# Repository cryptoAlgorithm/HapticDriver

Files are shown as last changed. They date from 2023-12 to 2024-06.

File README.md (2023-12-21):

# HapticDriver

> Compact and over-engineered solenoid driver board for the purpose of generating localised haptic feedback.

## Features

* ESP32S3 module
* USB-C host port
* 12 MOSFET H-bridges with current regulation (up to 1A each)
* Powered by LiPo batteries (15V max)
* Extremely compact size - approx 6x3cm including antenna
* 4-layer PCB

---

## Description

This is a _work in progress_ driver board which has the capability to drive 12 solenoids bi-directionally
for the purpose of providing focused and precise haptic feedback. It's intended to be used in tendem with
a host application communicating over either WiFi or Bluetooth.

Due to the ESP module's limited number of GPIO, 3 8-bit shift registers over I2S were used to effectively
expand 3 I2S GPIO into 24 individually assignable outputs. This corresponds to the 24 H-bridge driver
inputs, which allow powering 12 electromagnets (forming solenoids) with regulated current of either
direction.

There is a 3V3 LDO regulator onboard for powering the logic bus - including the ESP32, shift registers
and motor driver logic power. It's powered through the battery power input, and provides up to 800mA and
has an absolute maximum voltage of 15V. Although the drivers tolerate a power input of up to 18V, the
LDO effectively limits the maximum battery input voltage to 15V. Care should be taken not to exceed this.

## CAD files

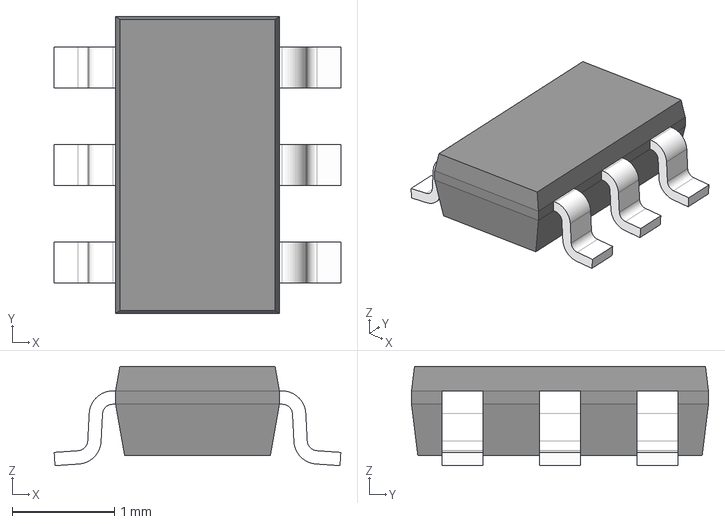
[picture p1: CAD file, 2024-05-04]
3DModels/DDC0006A.step
2.80 x 2.90 x 0.97 mm
BODY-SOT
LEAD-SOT x 6

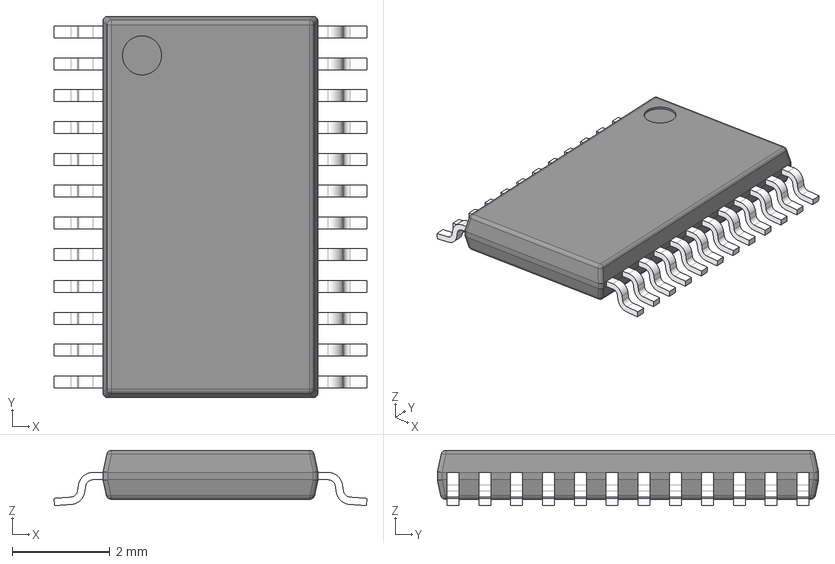
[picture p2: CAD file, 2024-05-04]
3DModels/PWP0024M.step
6.40 x 7.80 x 1.13 mm
BODY-TSSOP
LEAD-TSSOP x 24
PIN1
DAP

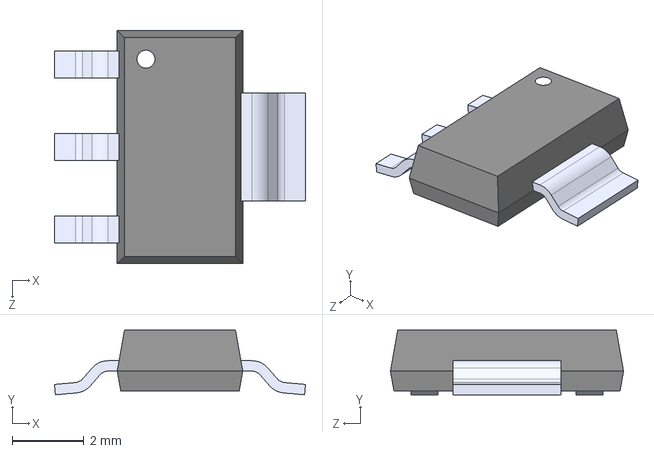
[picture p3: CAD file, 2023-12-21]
3DModels/REG1117-3.3.step
7.00 x 1.80 x 6.50 mm

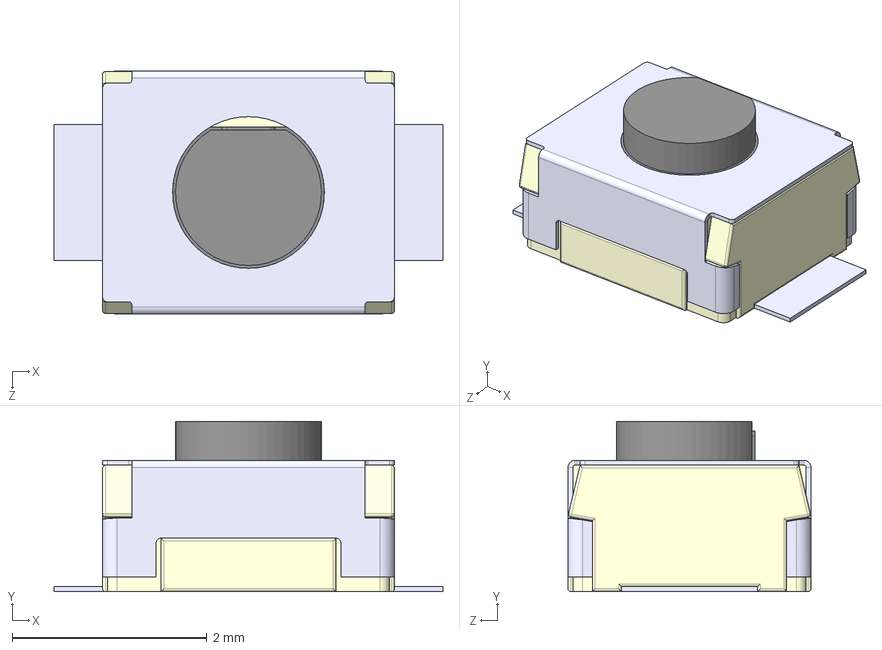
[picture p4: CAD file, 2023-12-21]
3DModels/B3U-1000P.step
4.00 x 1.75 x 2.50 mm

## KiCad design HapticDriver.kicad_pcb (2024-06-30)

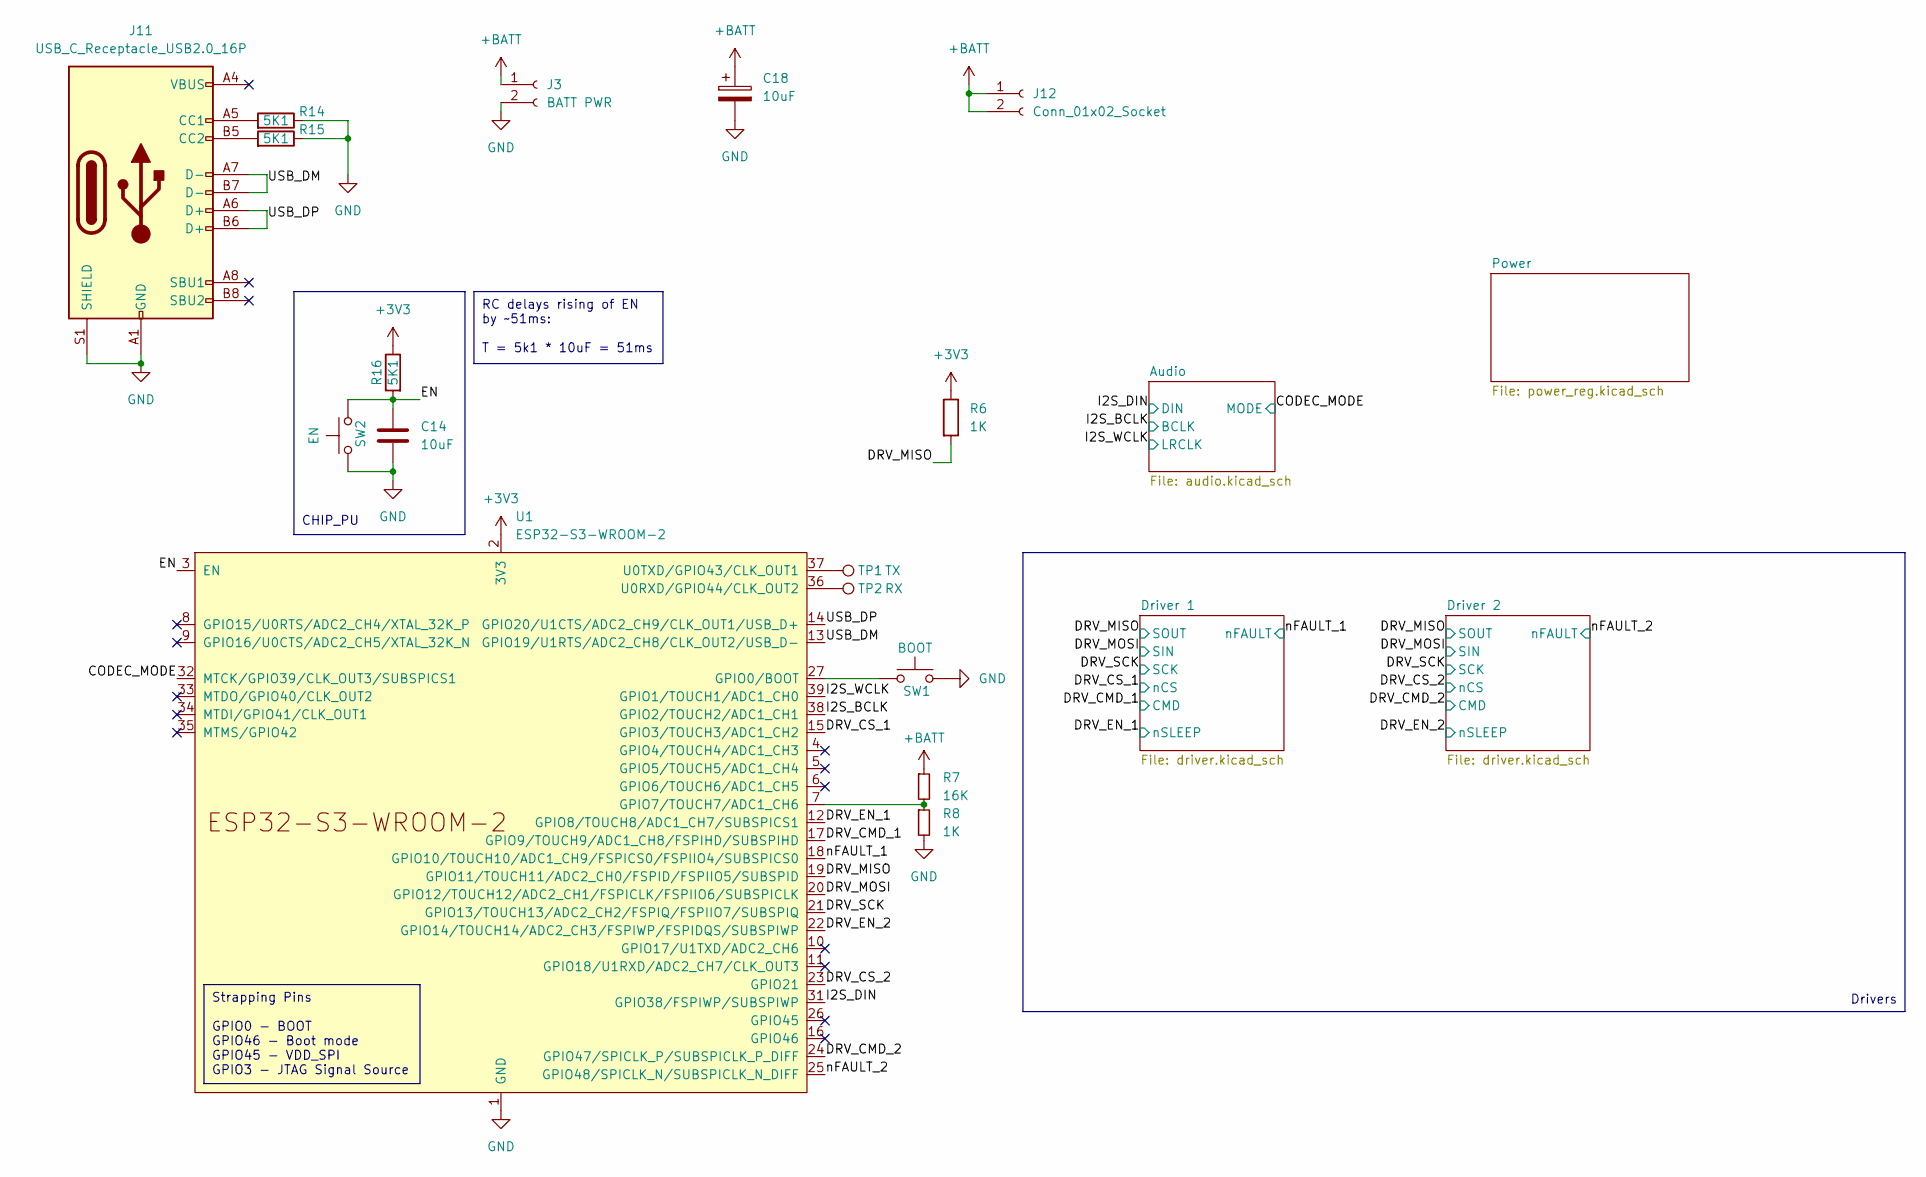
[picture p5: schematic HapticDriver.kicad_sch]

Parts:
C14: 10uF; C_0603_1608Metric; Part C96446
C18: 10uF; CP_Elec_4x5.4; Part C3001227
J3: BATT PWR; SolderWire-1sqmm_1x02_P5.4mm_D1.4mm_OD2.7mm
J11: USB_C_Receptacle_USB2.0_16P; USB_C_Receptacle_G-Switch_GT-USB-7010ASV; Part C2988369
J12: Conn_01x02_Socket; SolderWire_1x02
R6, R8: 1K; R_0402_1005Metric; Part C11702
R7: 16K; R_0402_1005Metric; Part C543609
R14, R15, R16: 5K1; R_0603_1608Metric; Part C2889415
SW1: BOOT; SW_Push_1P1T_XKB_TS-1187A; Part C318884
SW2: EN; SW_Push_1P1T_XKB_TS-1187A; Part C318884
TP1: TX; TestPoint_Pad_1.5x1.5mm
TP2: RX; TestPoint_Pad_1.5x1.5mm
U1: ESP32-S3-WROOM-2; ESP32-S3-WROOM-1; Part C2913202

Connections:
+3V3: R6.1, R16.1, U1.2 (3V3); also elsewhere on the board
+BATT: C18.1, J3.1, J12.1, J12.2, R7.1; also elsewhere on the board
/CODEC_MODE: U1.32 (MTCK/GPIO39/CLK_OUT3/SUBSPICS1); also elsewhere on the board
/DRV_CMD_1: U1.17 (GPIO9/TOUCH9/ADC1_CH8/FSPIHD/SUBSPIHD); also elsewhere on the board
/DRV_CMD_2: U1.24 (GPIO47/SPICLK_P/SUBSPICLK_P_DIFF); also elsewhere on the board
/DRV_CS_1: U1.15 (GPIO3/TOUCH3/ADC1_CH2); also elsewhere on the board
/DRV_CS_2: U1.23 (GPIO21); also elsewhere on the board
/DRV_EN_1: U1.12 (GPIO8/TOUCH8/ADC1_CH7/SUBSPICS1); also elsewhere on the board
/DRV_EN_2: U1.22 (GPIO14/TOUCH14/ADC2_CH3/FSPIWP/FSPIDQS/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); also elsewhere on the board
/DRV_MISO: R6.2, U1.19 (GPIO11/TOUCH11/ADC2_CH0/FSPID/FSPIIO5/S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); also elsewhere on the board
/DRV_MOSI: U1.20 (GPIO12/TOUCH12/ADC2_CH1/FSPICLK/FSPIIO6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); also elsewhere on the board
/DRV_SCK: U1.21 (GPIO13/TOUCH13/ADC2_CH2/FSPIQ/FSPIIO7/S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); also elsewhere on the board
/EN: C14.1, R16.2, SW2.2, U1.3 (EN)
/I2S_BCLK: U1.38 (GPIO2/TOUCH2/ADC1_CH1); also elsewhere on the board
/I2S_DIN: U1.31 (GPIO38/FSPIWP/SUBSPIWP); also elsewhere on the board
/I2S_WCLK: U1.39 (GPIO1/TOUCH1/ADC1_CH0); also elsewhere on the board
/USB_DM: J11.A7 (D-), J11.B7 (D-), U1.13 (GPIO19/U1RTS/ADC2_CH8/CLK_OUT2/USB_D-)
/USB_DP: J11.A6 (D+), J11.B6 (D+), U1.14 (GPIO20/U1CTS/ADC2_CH9/CLK_OUT1/USB_D+)
/nFAULT_1: U1.18 (GPIO10/TOUCH10/ADC1_CH9/FSPICS0/FSPIIO4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); also elsewhere on the board
/nFAULT_2: U1.25 (GPIO48/SPICLK_N/SUBSPICLK_N_DIFF); also elsewhere on the board
GND: C14.2, C18.2, J3.2, J11.A1 (GND), J11.A12 (GND), J11.B1 (GND), J11.B12 (GND), J11.S1 (SHIELD), R8.2, R14.1, R15.1, SW1.2, SW2.1, U1.1 (GND), U1.40 (GND), U1.41 (GND); also elsewhere on the board
unnamed: J11.A5 (CC1), R14.2
unnamed: J11.B5 (CC2), R15.2
unnamed: SW1.1, U1.27 (GPIO0/BOOT)
unnamed: R7.2, R8.1, U1.7 (GPIO7/TOUCH7/ADC1_CH6)
unnamed: TP2.1, U1.36 (U0RXD/GPIO44/CLK_OUT2)
unnamed: TP1.1, U1.37 (U0TXD/GPIO43/CLK_OUT1)

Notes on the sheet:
Strapping Pins GPIO0 - BOOT GPIO46 - Boot mode GPIO45 - VDD_SPI GPIO3 - JTAG Signal Source
RC delays rising of EN by ~51ms: T = 5k1 * 10uF = 51ms
Drivers
CHIP_PU

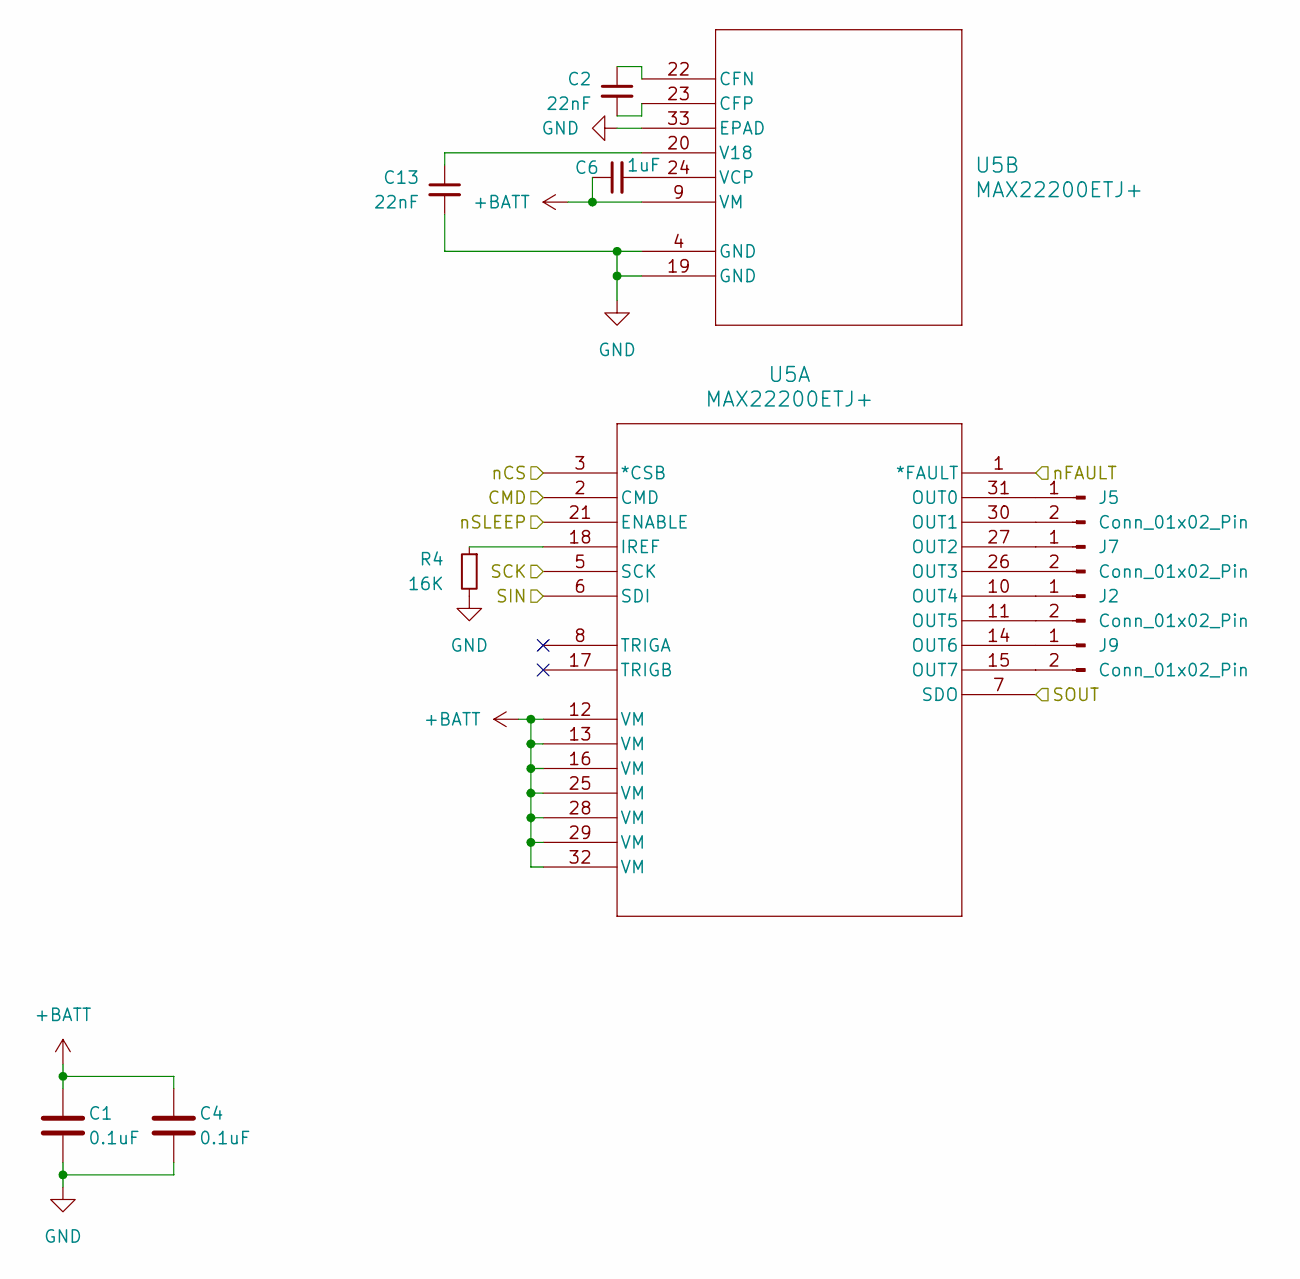
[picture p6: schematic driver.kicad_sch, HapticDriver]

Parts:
C1, C4: 0.1uF; C_0603_1608Metric; Part C14663
C2, C13: 22nF; C_0402_1005Metric; Part C1532
C6: 1uF; C_0402_1005Metric; Part C52923
J2, J5, J7, J9: Conn_01x02_Pin; SolderWire_1x02
R4: 16K; R_0402_1005Metric; Part C543609
U5: MAX22200ETJ+; 21-0140AK_T3255_8C_MXM; Part C2845158

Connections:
+BATT: C1.1, C4.1, C6.1, U5.9 (VM), U5.12 (VM), U5.13 (VM), U5.16 (VM), U5.25 (VM), U5.28 (VM), U5.29 (VM), U5.32 (VM); also elsewhere on the board
/DRV_CMD_1: U5.2 (CMD); also elsewhere on the board
/DRV_CS_1: U5.3 (*CSB); also elsewhere on the board
/DRV_EN_1: U5.21 (ENABLE); also elsewhere on the board
/DRV_MISO: U5.7 (SDO); also elsewhere on the board
/DRV_MOSI: U5.6 (SDI); also elsewhere on the board
/DRV_SCK: U5.5 (SCK); also elsewhere on the board
/nFAULT_1: U5.1 (*FAULT); also elsewhere on the board
GND: C1.2, C4.2, C13.2, R4.2, U5.4 (GND), U5.19 (GND), U5.33 (EPAD); also elsewhere on the board
unnamed: J2.1, U5.10 (OUT4)
unnamed: J2.2, U5.11 (OUT5)
unnamed: J5.1, U5.31 (OUT0)
unnamed: J5.2, U5.30 (OUT1)
unnamed: J7.1, U5.27 (OUT2)
unnamed: J7.2, U5.26 (OUT3)
unnamed: J9.1, U5.14 (OUT6)
unnamed: J9.2, U5.15 (OUT7)
unnamed: R4.1, U5.18 (IREF)
unnamed: C2.1, U5.22 (CFN)
unnamed: C2.2, U5.23 (CFP)
unnamed: C13.1, U5.20 (V18)
unnamed: C6.2, U5.24 (VCP)

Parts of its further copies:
C3, C12: 0.1uF; C_0603_1608Metric; Part C14663
C5, C15: 22nF; C_0402_1005Metric; Part C1532
C9: 1uF; C_0402_1005Metric; Part C52923
J4, J6, J8, J10: Conn_01x02_Pin; SolderWire_1x02
R5: 16K; R_0402_1005Metric; Part C543609
U6: MAX22200ETJ+; 21-0140AK_T3255_8C_MXM; Part C2845158

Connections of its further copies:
+BATT: C3.1, C9.1, C12.1, U6.9 (VM), U6.12 (VM), U6.13 (VM), U6.16 (VM), U6.25 (VM), U6.28 (VM), U6.29 (VM), U6.32 (VM); also elsewhere on the board
/DRV_CMD_2: U6.2 (CMD); also elsewhere on the board
/DRV_CS_2: U6.3 (*CSB); also elsewhere on the board
/DRV_EN_2: U6.21 (ENABLE); also elsewhere on the board
/DRV_MISO: U6.7 (SDO); also elsewhere on the board
/DRV_MOSI: U6.6 (SDI); also elsewhere on the board
/DRV_SCK: U6.5 (SCK); also elsewhere on the board
/nFAULT_2: U6.1 (*FAULT); also elsewhere on the board
GND: C3.2, C12.2, C15.2, R5.2, U6.4 (GND), U6.19 (GND), U6.33 (EPAD); also elsewhere on the board
unnamed: J4.1, U6.10 (OUT4)
unnamed: J4.2, U6.11 (OUT5)
unnamed: J6.1, U6.31 (OUT0)
unnamed: J6.2, U6.30 (OUT1)
unnamed: J8.1, U6.27 (OUT2)
unnamed: J8.2, U6.26 (OUT3)
unnamed: J10.1, U6.14 (OUT6)
unnamed: J10.2, U6.15 (OUT7)
unnamed: R5.1, U6.18 (IREF)
unnamed: C5.1, U6.22 (CFN)
unnamed: C5.2, U6.23 (CFP)
unnamed: C15.1, U6.20 (V18)
unnamed: C9.2, U6.24 (VCP)

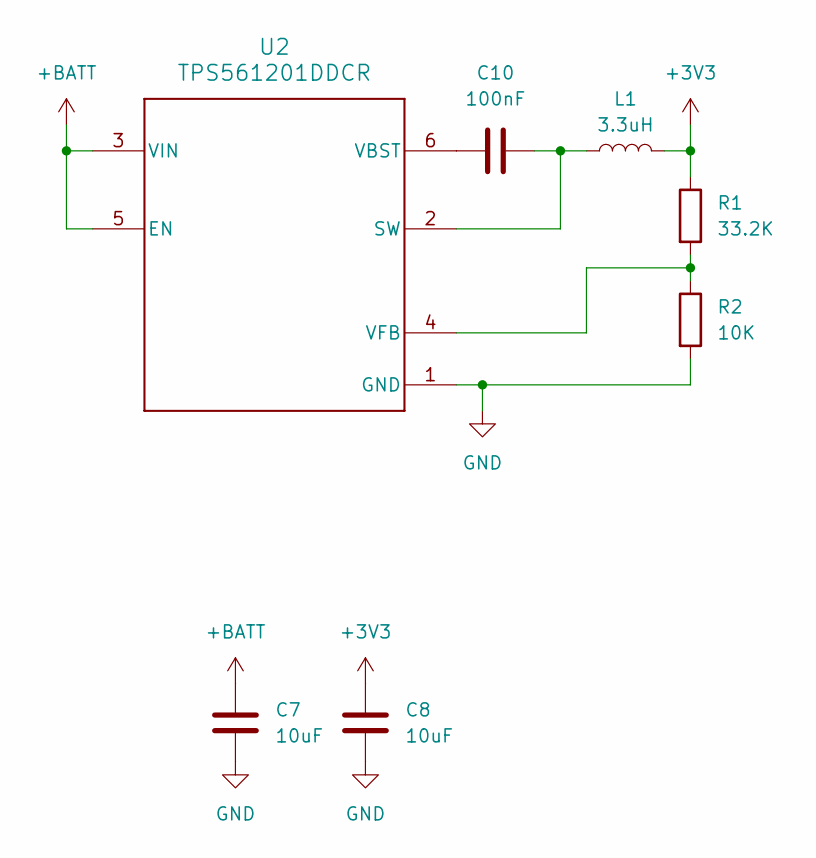
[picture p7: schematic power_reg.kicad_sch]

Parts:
C7, C8: 10uF; C_1206_3216Metric_Pad1.33x1.80mm_HandSolder; Part C13585
C10: 100nF; C_0603_1608Metric; Part C14663
L1: 3.3uH; L_Changjiang_FXL0530-3R3-M; Part C475518
R1: 33.2K; R_0603_1608Metric; Part C4216
R2: 10K; R_0603_1608Metric; Part C25804
U2: TPS561201DDCR; DDC0006A_N; Part C220433

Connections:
+3V3: C8.1, L1.2, R1.1; also elsewhere on the board
+BATT: C7.1, U2.3 (VIN), U2.5 (EN); also elsewhere on the board
GND: C7.2, C8.2, R2.2, U2.1 (GND); also elsewhere on the board
unnamed: C10.2, L1.1, U2.2 (SW)
unnamed: C10.1, U2.6 (VBST)
unnamed: R1.2, R2.1, U2.4 (VFB)

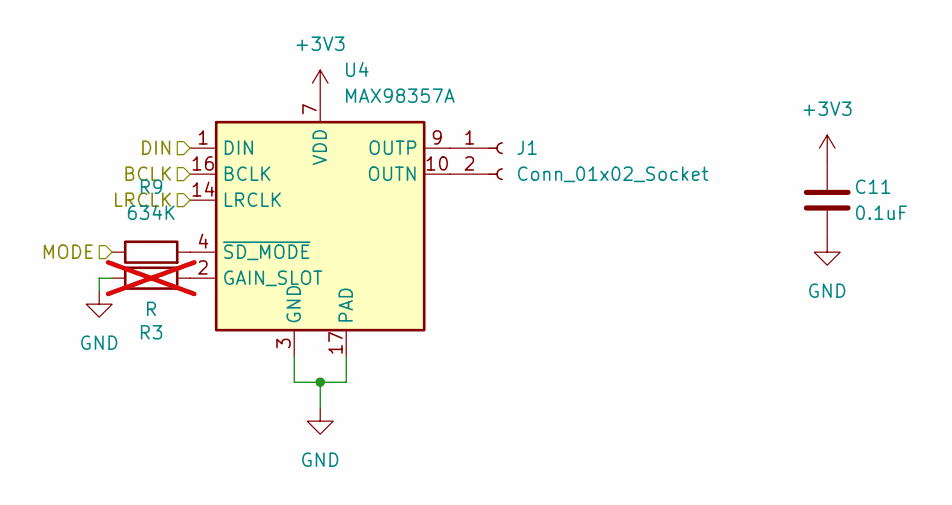
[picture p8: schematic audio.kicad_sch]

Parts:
C11: 0.1uF; C_0603_1608Metric; Part C14663
J1: Conn_01x02_Socket; SolderWire_1x02
R3: R; R_0402_1005Metric; not fitted
R9: 634K; R_0402_1005Metric; Part C227175
U4: MAX98357A; TQFN-16-1EP_3x3mm_P0.5mm_EP1.23x1.23mm; Part C910544

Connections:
+3V3: C11.1, U4.7 (VDD), U4.8 (VDD); also elsewhere on the board
/CODEC_MODE: R9.1; also elsewhere on the board
/I2S_BCLK: U4.16 (BCLK); also elsewhere on the board
/I2S_DIN: U4.1 (DIN); also elsewhere on the board
/I2S_WCLK: U4.14 (LRCLK); also elsewhere on the board
GND: C11.2, R3.1, U4.3 (GND), U4.11 (GND), U4.15 (GND), U4.17 (PAD); also elsewhere on the board
unnamed: J1.1, U4.9 (OUTP)
unnamed: J1.2, U4.10 (OUTN)
unnamed: R3.2, U4.2 (GAIN_SLOT)
unnamed: R9.2, U4.4 (~SD_MODE)

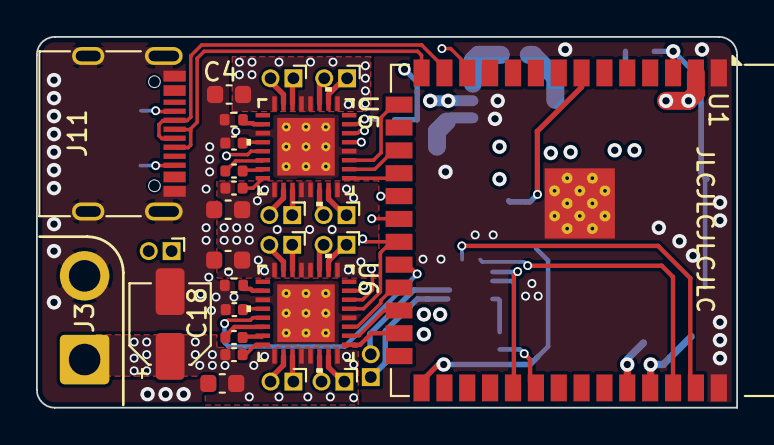
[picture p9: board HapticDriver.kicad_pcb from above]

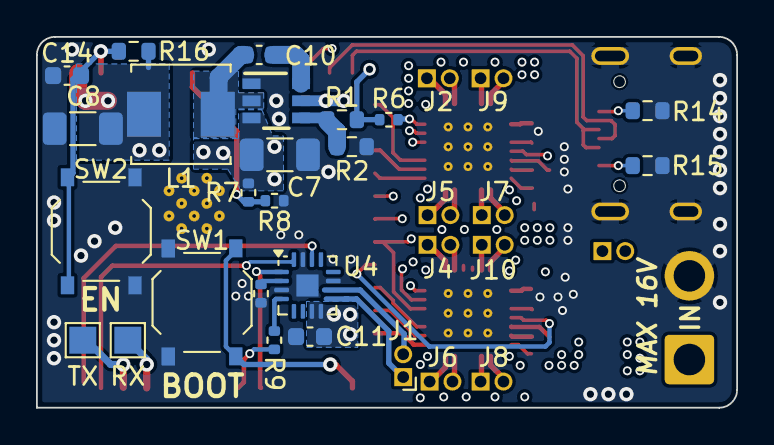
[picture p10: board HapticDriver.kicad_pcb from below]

Board: 4 copper layers, 38.9 x 20.6 mm, 50 parts (23 on the bottom side), 60 nets.

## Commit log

2023-12-21 feat: intial commit, mostly complete v0.1 design
    [B3U-1000P.step, HapticDriver.kicad_pcb, HapticDriver.kicad_sch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]
2023-12-21 patch: ignore KiCad working files
2023-12-21 feat: pull OE and CLR shift reg pins to correct voltages
    [HapticDriver.kicad_pcb, HapticDriver.kicad_sch]
2023-12-21 patch: mark unused pins
    [HapticDriver.kicad_pcb, HapticDriver.kicad_sch, driver.kicad_sch]
2023-12-22 fix: avoid SDA on strapping pin GPIO45
    [HapticDriver.kicad_pcb, HapticDriver.kicad_sch]
2023-12-22 patch: specify value of sense resistor
    [HapticDriver.kicad_pcb, driver.kicad_sch]
2023-12-22 fix: delay rising of EN with cap, as per devkit design
    [HapticDriver.kicad_pcb, HapticDriver.kicad_sch]
2023-12-22 patch: improve silkscreen, add testpoints, optimise some traces
    [HapticDriver.kicad_pcb, HapticDriver.kicad_sch]
2023-12-23 patch: final touch-ups, v0.1 fabrication
    [HapticDriver.kicad_pcb, HapticDriver.kicad_sch]
2024-05-04 feat: major redesign with better driver and audio, partial routing
    [DDC0006A.step, HapticDriver.kicad_pcb, HapticDriver.kicad_sch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]
2024-05-28 feat: full reroute with max22200 driver
    [HapticDriver.kicad_pcb, HapticDriver.kicad_sch, audio.kicad_sch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]
2024-05-29 feat: fully routed v2 design
    [HapticDriver.kicad_pcb, HapticDriver.kicad_sch, driver.kicad_sch]
2024-06-27 feat: battery level measurement resistors
    [HapticDriver.kicad_pcb, HapticDriver.kicad_sch, driver.kicad_sch]
2024-06-30 feat: populate all jlcpcb part#
    [HapticDriver.kicad_pcb, HapticDriver.kicad_sch, audio.kicad_sch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]
